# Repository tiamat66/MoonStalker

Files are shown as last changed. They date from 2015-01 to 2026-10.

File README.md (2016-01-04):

# MoonStalker

**Software for GoTo telescope control**

## Purpose

Project for GoTo telescope control consists of hardware and software. Software lives in this repository. There are two pieces of software.
 
The first called Drive is used on an arduino based platform that drives the hardwares GoTo feature and uses stepper motors.

The second piece called Control is Android based software that commands the Drive software and contains the user interface and logic.

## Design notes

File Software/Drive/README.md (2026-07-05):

# Drive

## Purpose

Drive is a software component installed on an Arduino Micro based hardware, which controls the stepper motors that rotate the telescope and provide GoTo and track functionality.

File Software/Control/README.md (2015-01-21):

# Control

## Purpose

Control is an Android application that communicates with an Arduino based hardware that drives the telescope. Communication between Android device and Arduino platform is performed over a Bluetooth connection.

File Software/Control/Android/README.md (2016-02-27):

# Android

## Purpose

Android application.
Includes an user friendly interface and module for Telescope positioning calculation.
It also includes module for Bluetooth connection with Arduino platform.

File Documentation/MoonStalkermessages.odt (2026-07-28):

MoonStalker messages

# Introduction

This document describes the messages being exchanged between the Android Control and the Arduino based Drive unit.

< - start message delimiter

> - end message delimiter

All messages exchanged must start with the start message delimiter and end with the end message delimiter, e.g. <BTRY?> to query the battery voltage. Carriage return '\r' and newline '\n' can be sent, but will be ignored and removed from the text stream. All text is ASCII encoded.

Android Control is the initiator of messages and Arduino Drive unit responds to the messages to acknowledge receipt and provide responses. The only exception are the error, warning and info messages, which can be sent to the Android Control unit unsolicited.

# Control messages

## Move

<MV a b s> IDLE -> WAITING

a - horizontal steps

b - vertical steps

s – maximum speed of the stepper in RPM

Move the telescope in horizontal and vertical direction. While RDY message is not returned from Arduino, all move actions made by MoonStalker are blocked. The maximum speed for the stepper motors is specified with s, e.g. 500 RPM.

Example:

<MV 1000 200 500>

Moves 1000 steps in horizontal and 200 steps in vertical. Horizontal will move with 500 RPM, vertical will move with 100 RPM, because it needs to execute five times less steps.

Response:

<MV_ACK a b s> - Start movement with the specified parameters WAITING -> MOVING

<RDY> - Finished moving to spec location, MOVING -> IDLE ... gre na ping receiver

## Move start

<MVS d s --> IDLE --> WAITING

d - direction (N, S, W, E, NW, NE, SW, SE)

s – speed in RPM, both horiz and vertical steppers move with this speed

Start moving the telescope in the specific direction. It keeps moving until MVE message is received or ERROR happens. Speed s is specified in RPM of the stepper motor.

Example:

<MVS NE 500>

Starts moving both horizontal and vertical stepper to move the telescope in NE direction (up and to the right), both steppers rotate with 500 RPM.

Response:

<MVS_ACK d s> - Start movement with the specified parameters WAITING -> MOVING

<NOT_RDY> - Drive unit is not currently executing MVS started movement

## Move end

<MVE> MOVING -> WAITING

Stop moving the telescope after started when MVS was received.

Response:

<NOT_RDY> - Drive unit is not currently executing MVS started movement

<MVE_ACK> - Stopping previously started MVS movement WAITING -> IDLE

# Status messages

## Status

<MVST?> -> WAITING

Get move status of the telescope, whether the telescope is still moving or if it is ready to accept new move command.

Response:

<RDY> - Drive unit is ready to accept new move command

<NOT_RDY> - Drive unit is still executing the previous move command and is not ready yet to accept new move commands

## Battery

<BTRY?>

Request to Arduino to return the battery voltage in mV.

Response:

<BTRY voltage>

voltage - value of the current voltage of Telescope battery in millivolts.

Reply from Arduino give information of current voltage of telescope battery.

# Error Messages

Error messages can be sent to the Android Control unit unsolicited.

<ERROR error_msg>

When something unexpected happens on telescope, the reason for error is returned from Arduino.

ERROR MESSAGE | MEANING
END_LIMIT_SW_TRIG | End limit switch has been triggered

# Warning messages

Warning messages can be sent to the Android Control unit unsolicited.

<WARNING warning_msg>

WARNING MESSAGE | MEANING
BTRY_LOW | Battery voltage is low

# Info messages

Info messages can be sent to the Android Control unit unsolicited.

Info messages can be anything and are only meant for logging purposes. The Control unit is not meant to execute any actions upon receiving them.

<INFO info_msg>

# Position messages

An azimuth and height in degrees are sent to FE app of current object

<POS pos_msg>

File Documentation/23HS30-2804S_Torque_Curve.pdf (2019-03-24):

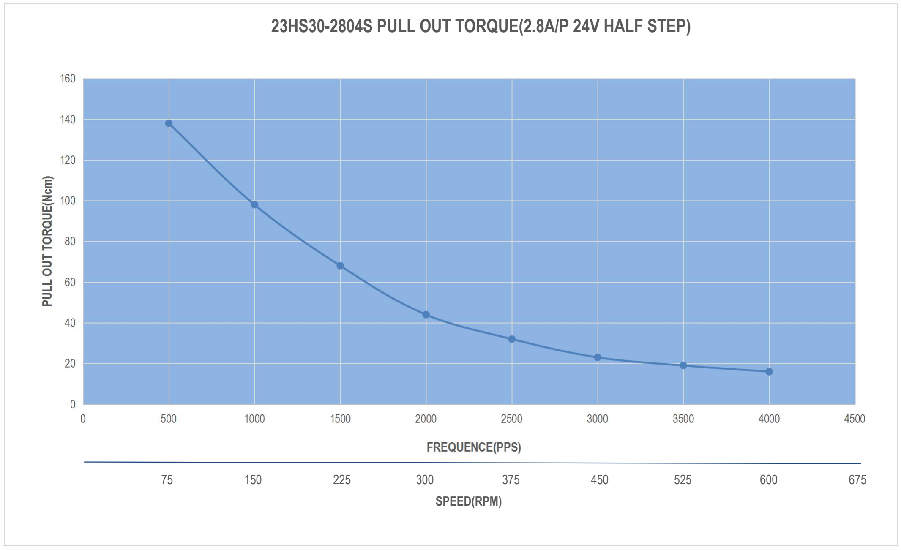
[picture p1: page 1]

23HS30-2804S PULL OUT TORQUE(2.8A/P 24V HALF STEP)

75 | 150 | 225 | 300 | 375 | 450 | 525 | 600 | 675
SPEED(RPM)

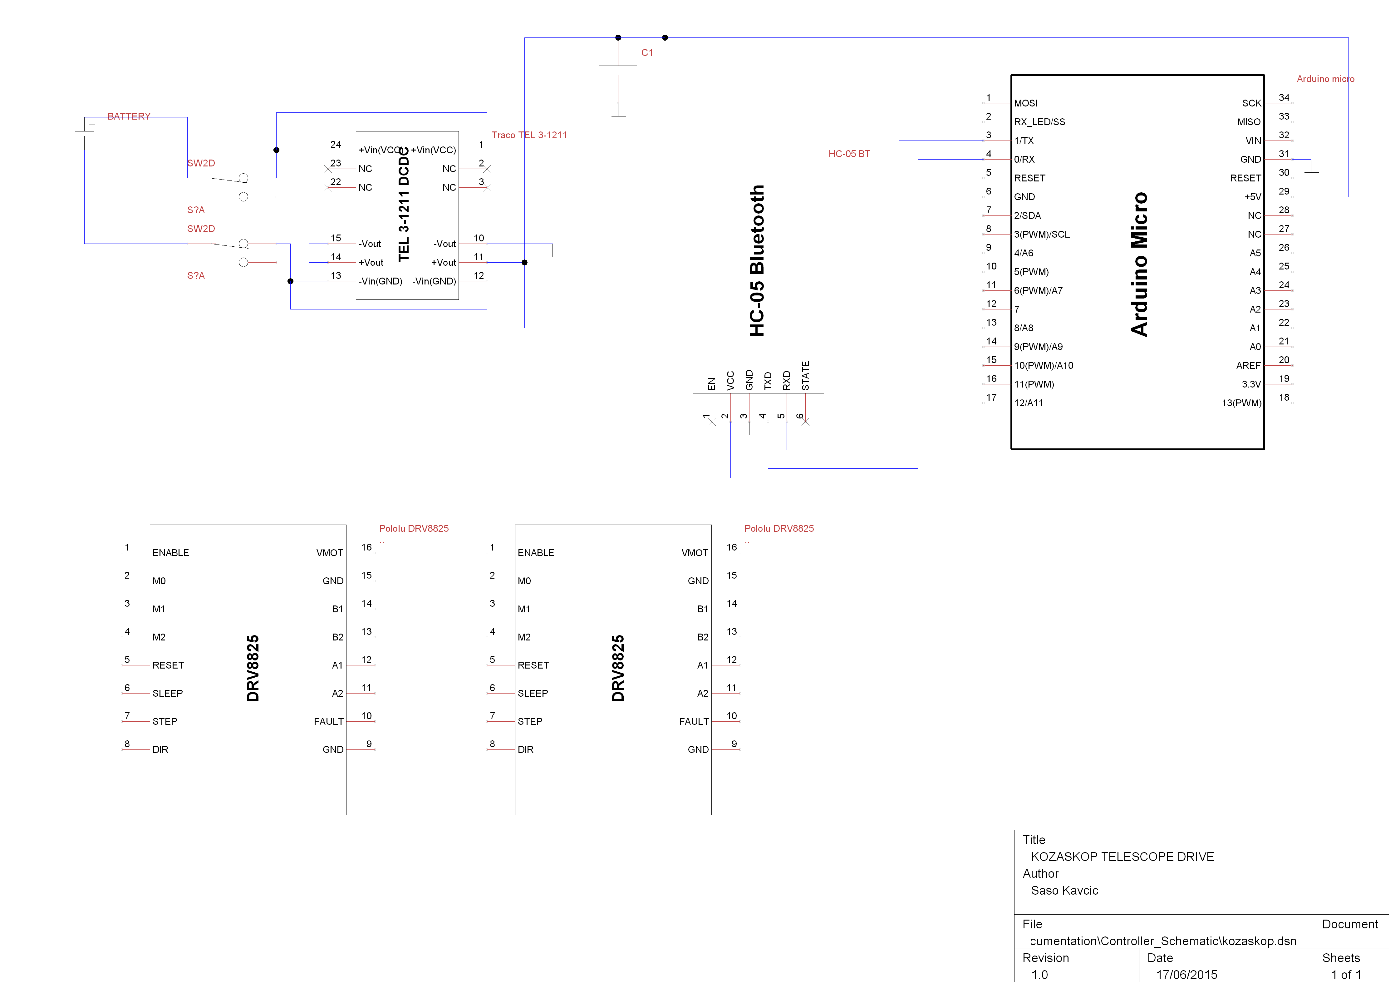
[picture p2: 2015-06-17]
Documentation/Controller_Schematic/kozaskop.png

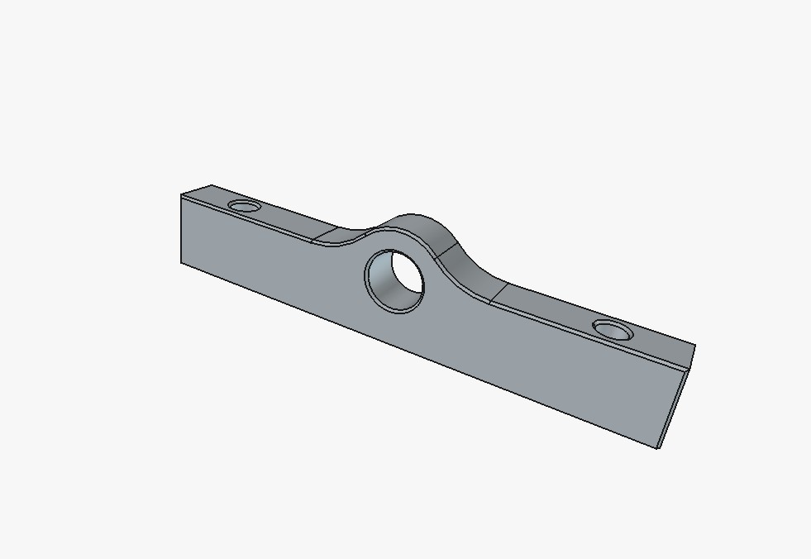
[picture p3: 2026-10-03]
CAD/tube_holder/tube_holder.jpeg

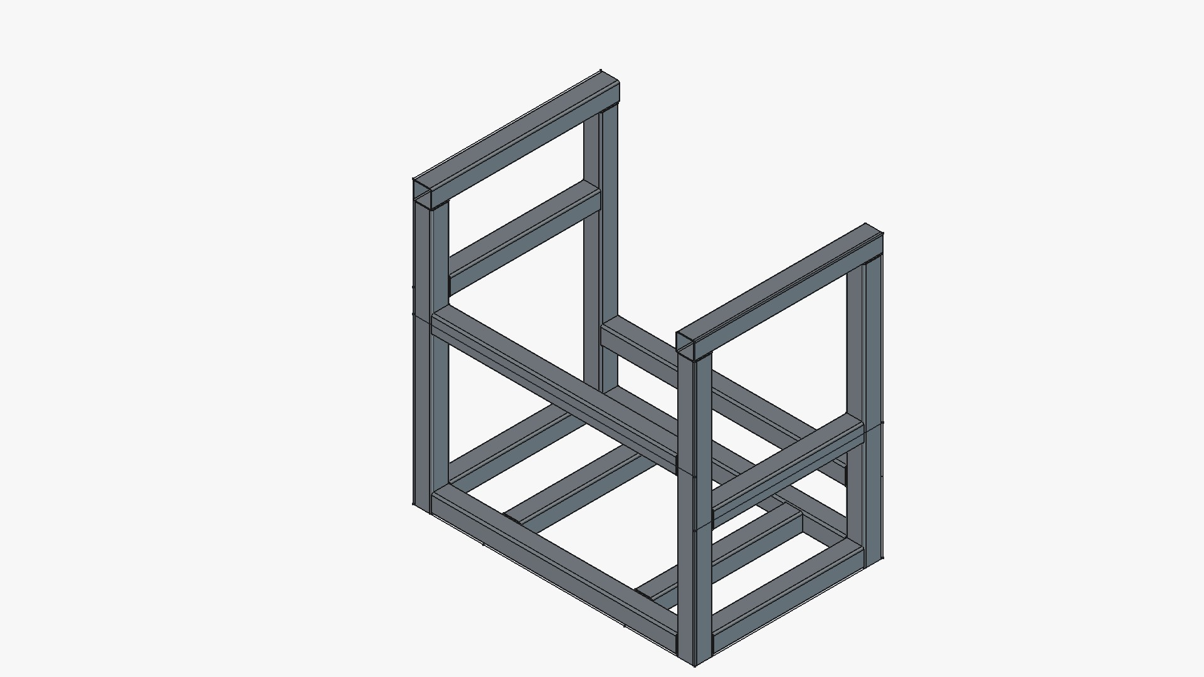
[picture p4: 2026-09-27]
CAD/upper_frame/upper_frame.jpeg

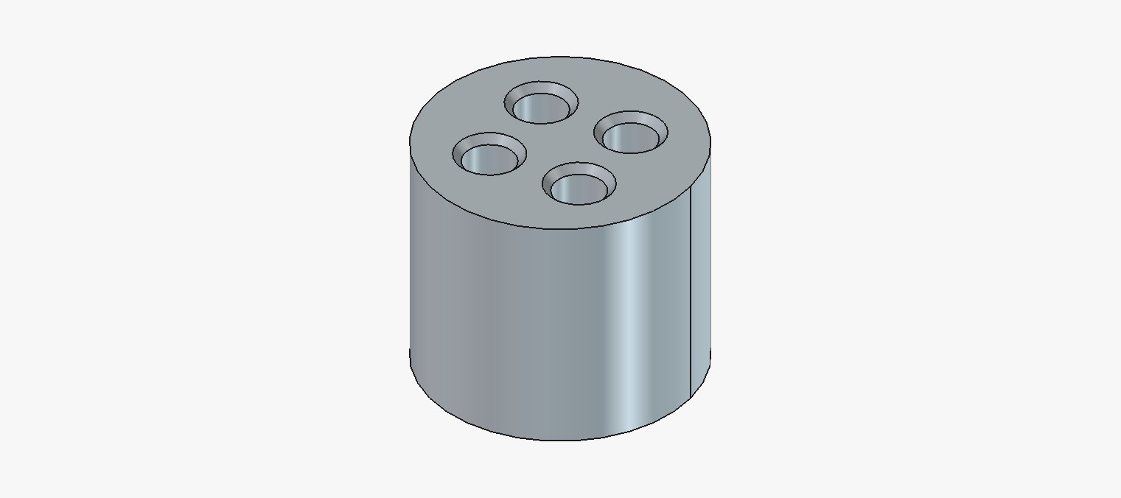
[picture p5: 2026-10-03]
CAD/spool/spool.jpeg

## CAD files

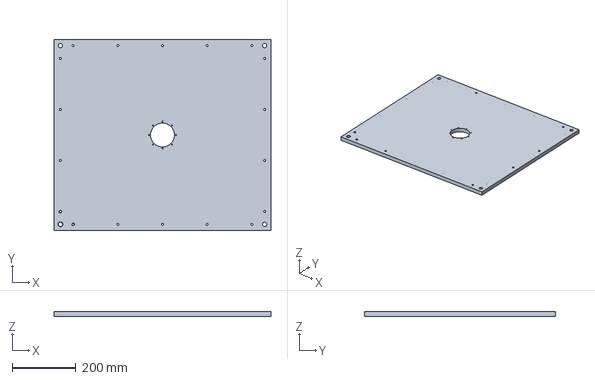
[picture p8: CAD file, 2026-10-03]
CAD/bottom_plate/bottom_plate.FCStd
680.0 x 600.0 x 15.0 mm

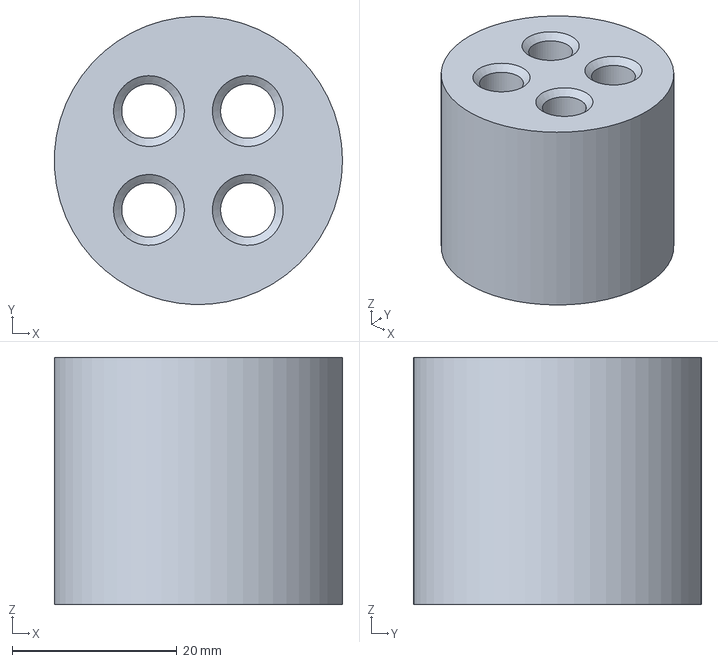
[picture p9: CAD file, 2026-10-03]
CAD/spool/spool.FCStd
35.0 x 35.0 x 30.0 mm

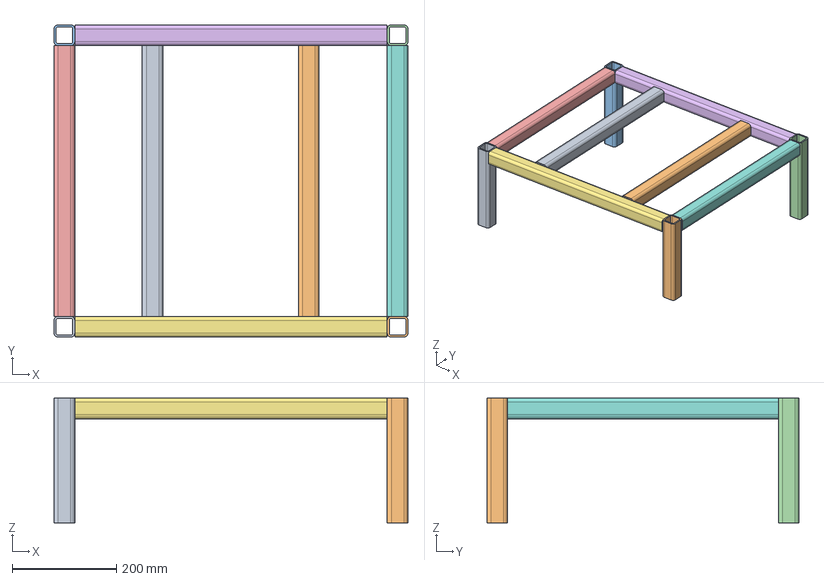
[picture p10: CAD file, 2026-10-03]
CAD/stand/stand.FCStd
680.0 x 600.0 x 240.0 mm
Profile_40x4_0_029
Profile_40x4_0_033
Profile_40x4_0_037
Profile_40x4_0_041
Profile_40x4_0_004_Tr_Tr
Profile_40x4_0_007_Tr_Tr
Profile_40x4_0_006_Tr_Tr
Profile_40x4_0_005_Tr_Tr
Profile_40x4_0_020_Tr
Profile_40x4_0_021_Tr

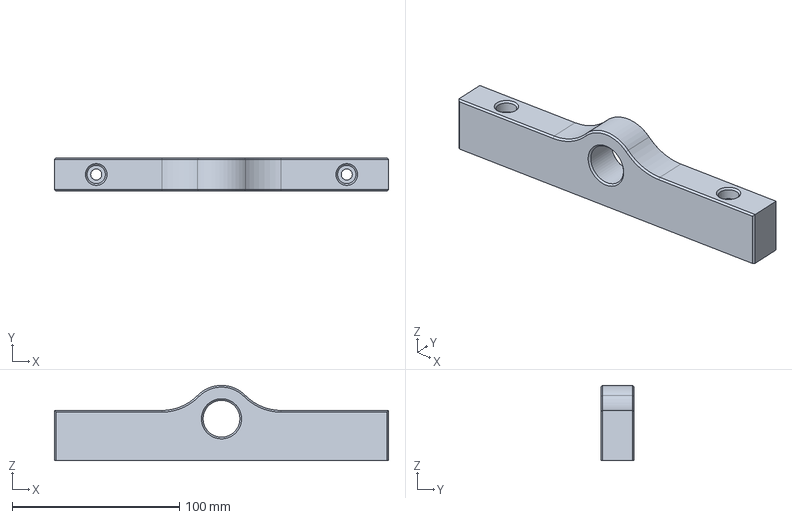
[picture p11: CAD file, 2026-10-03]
CAD/tube_holder/tube_holder.FCStd
200.0 x 20.0 x 45.0 mm

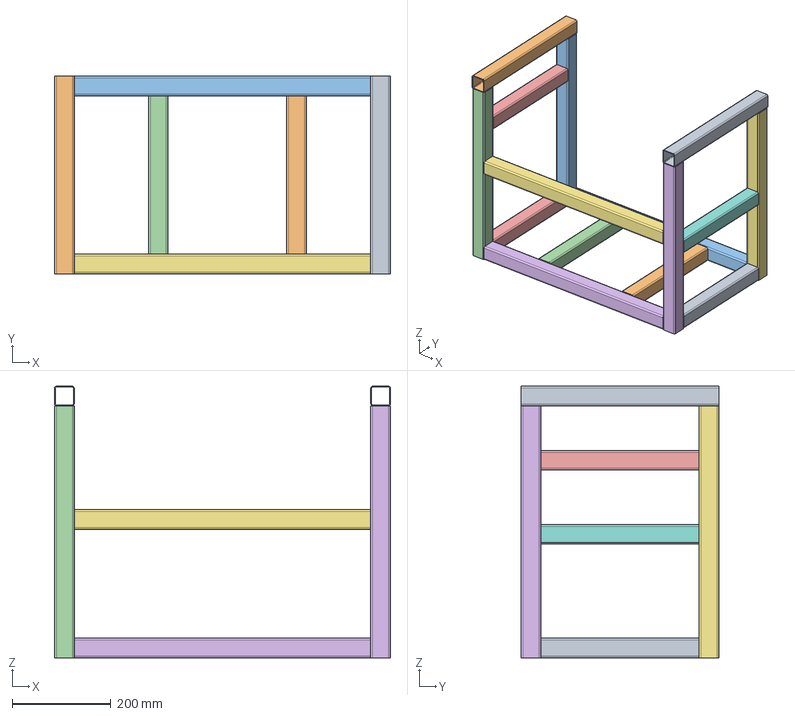
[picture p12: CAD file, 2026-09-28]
CAD/upper_frame/upper_frame.FCStd
680.0 x 400.0 x 550.0 mm
Profile_40x2_0_002
Profile_40x2_0_003
Profile_40x2_0_044_Tr
Profile_40x2_0_010_Tr
Profile_40x2_0_040_Tr_Tr001
Profile_40x2_0_011_Tr002
Profile_40x2_0_041_Tr_Tr001
Profile_40x2_0_043_Tr_Tr001
Profile_40x2_0_028_Tr_Tr002
Profile_40x2_0_031_Tr_Tr001
Profile_40x2_0_027_Tr_Tr001
Profile_40x2_0_030_Tr_Tr001
Profile_40x2_0_026_Tr_Tr001
Profile_40x2_0_029_Tr_Tr001
Profile_40x2_0_045_Tr

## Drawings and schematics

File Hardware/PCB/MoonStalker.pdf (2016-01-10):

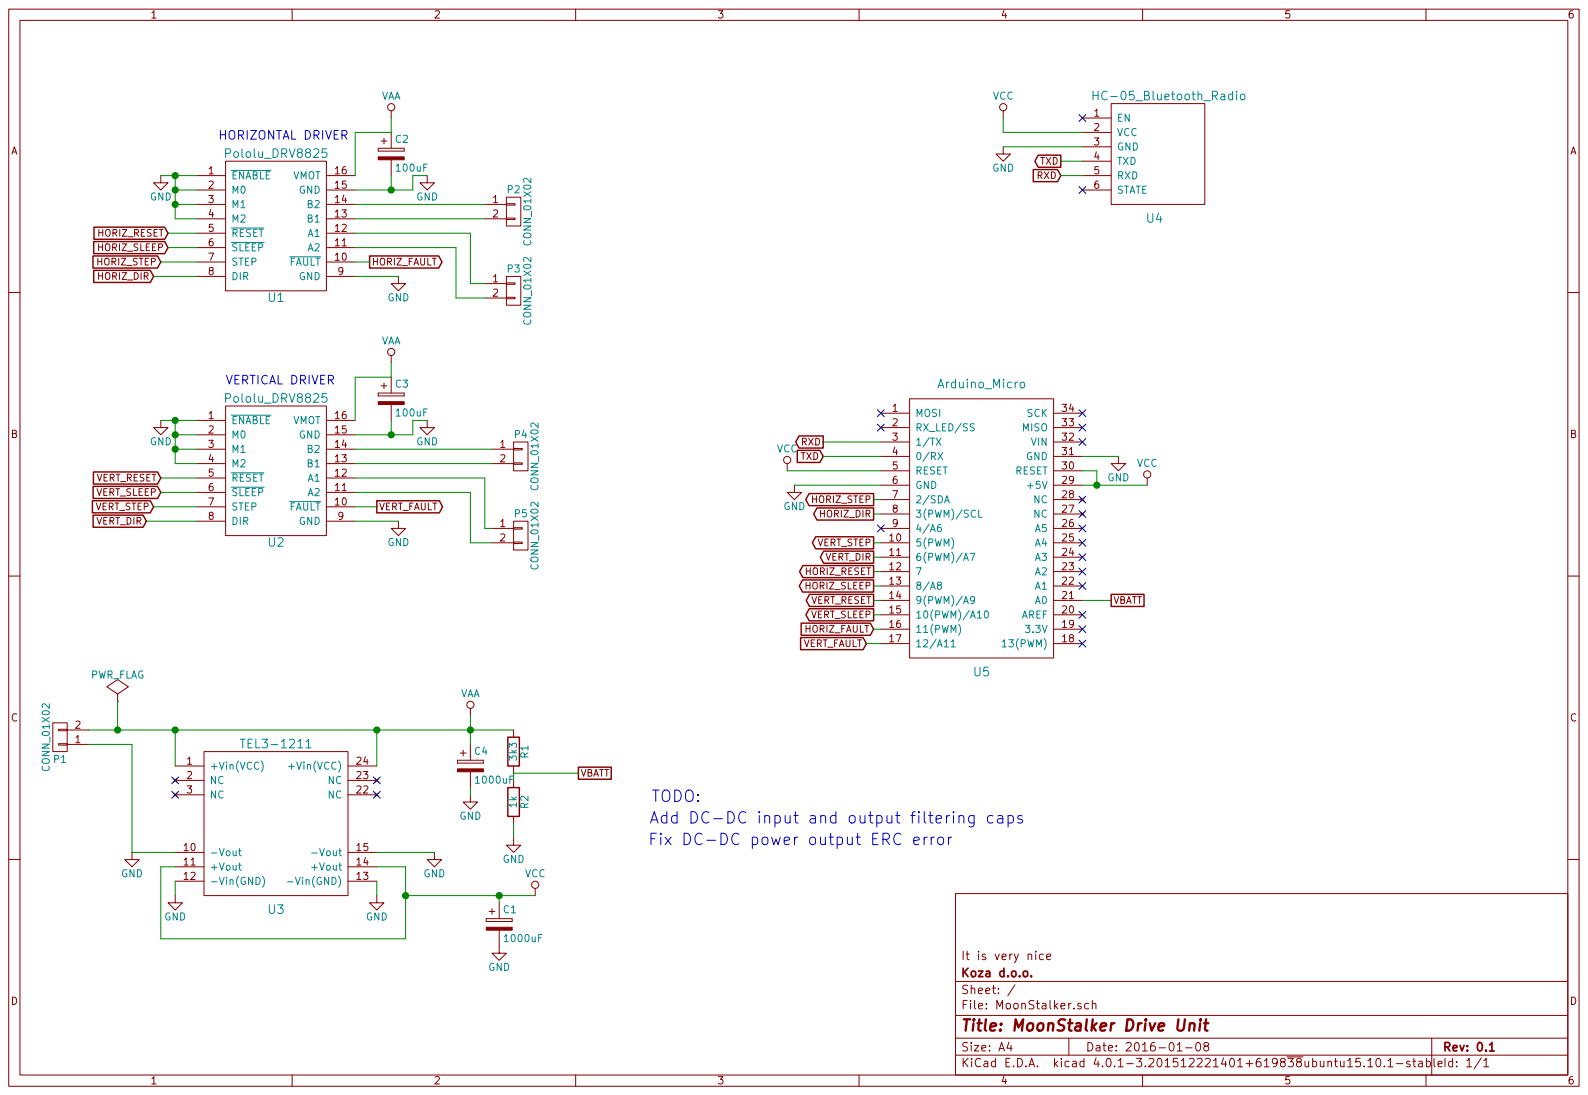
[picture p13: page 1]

Add DC-DC input and output filtering caps

Id: 1/1 Title: MoonStalker Drive Unit File: MoonStalker.sch Sheet: / Koza d.o.o.

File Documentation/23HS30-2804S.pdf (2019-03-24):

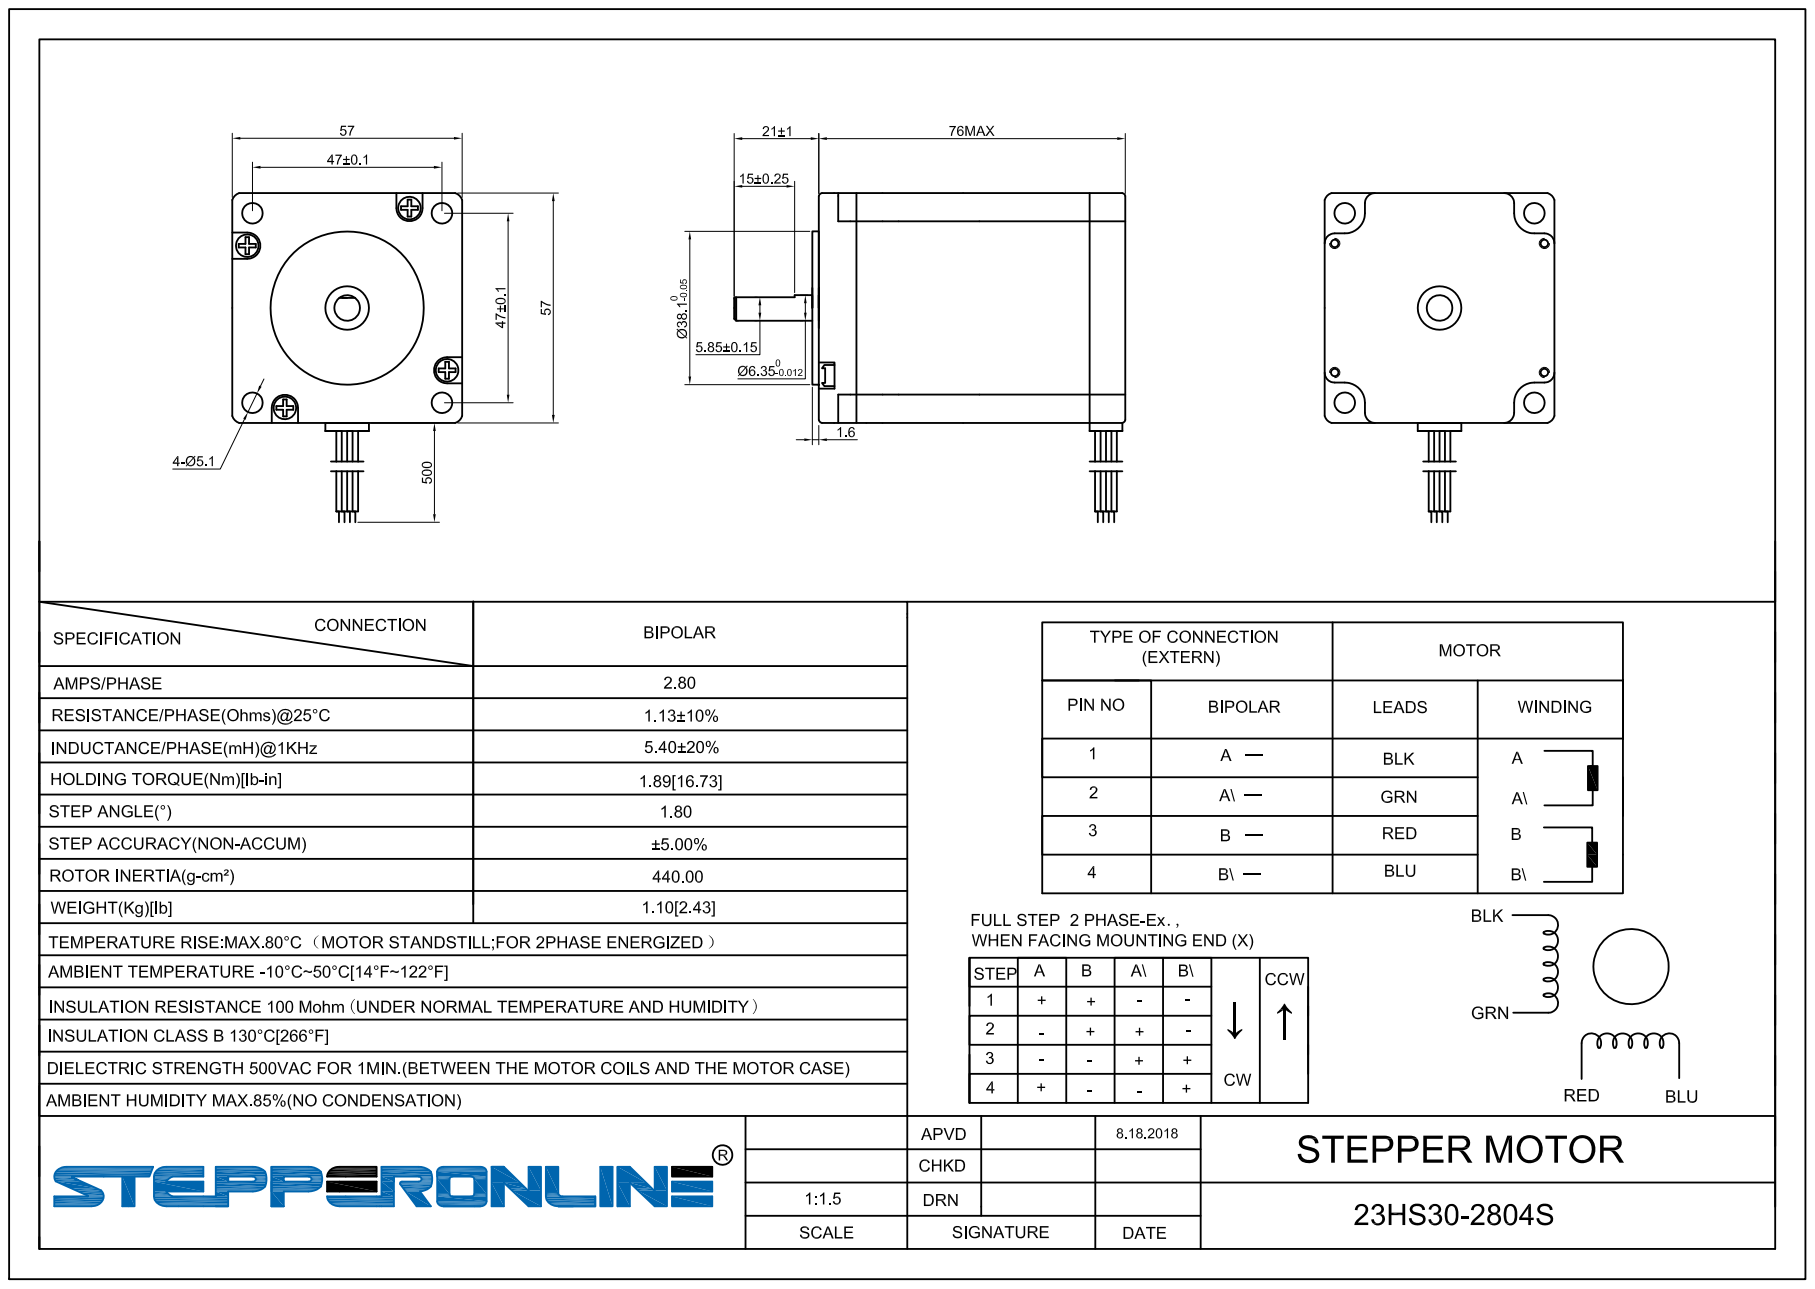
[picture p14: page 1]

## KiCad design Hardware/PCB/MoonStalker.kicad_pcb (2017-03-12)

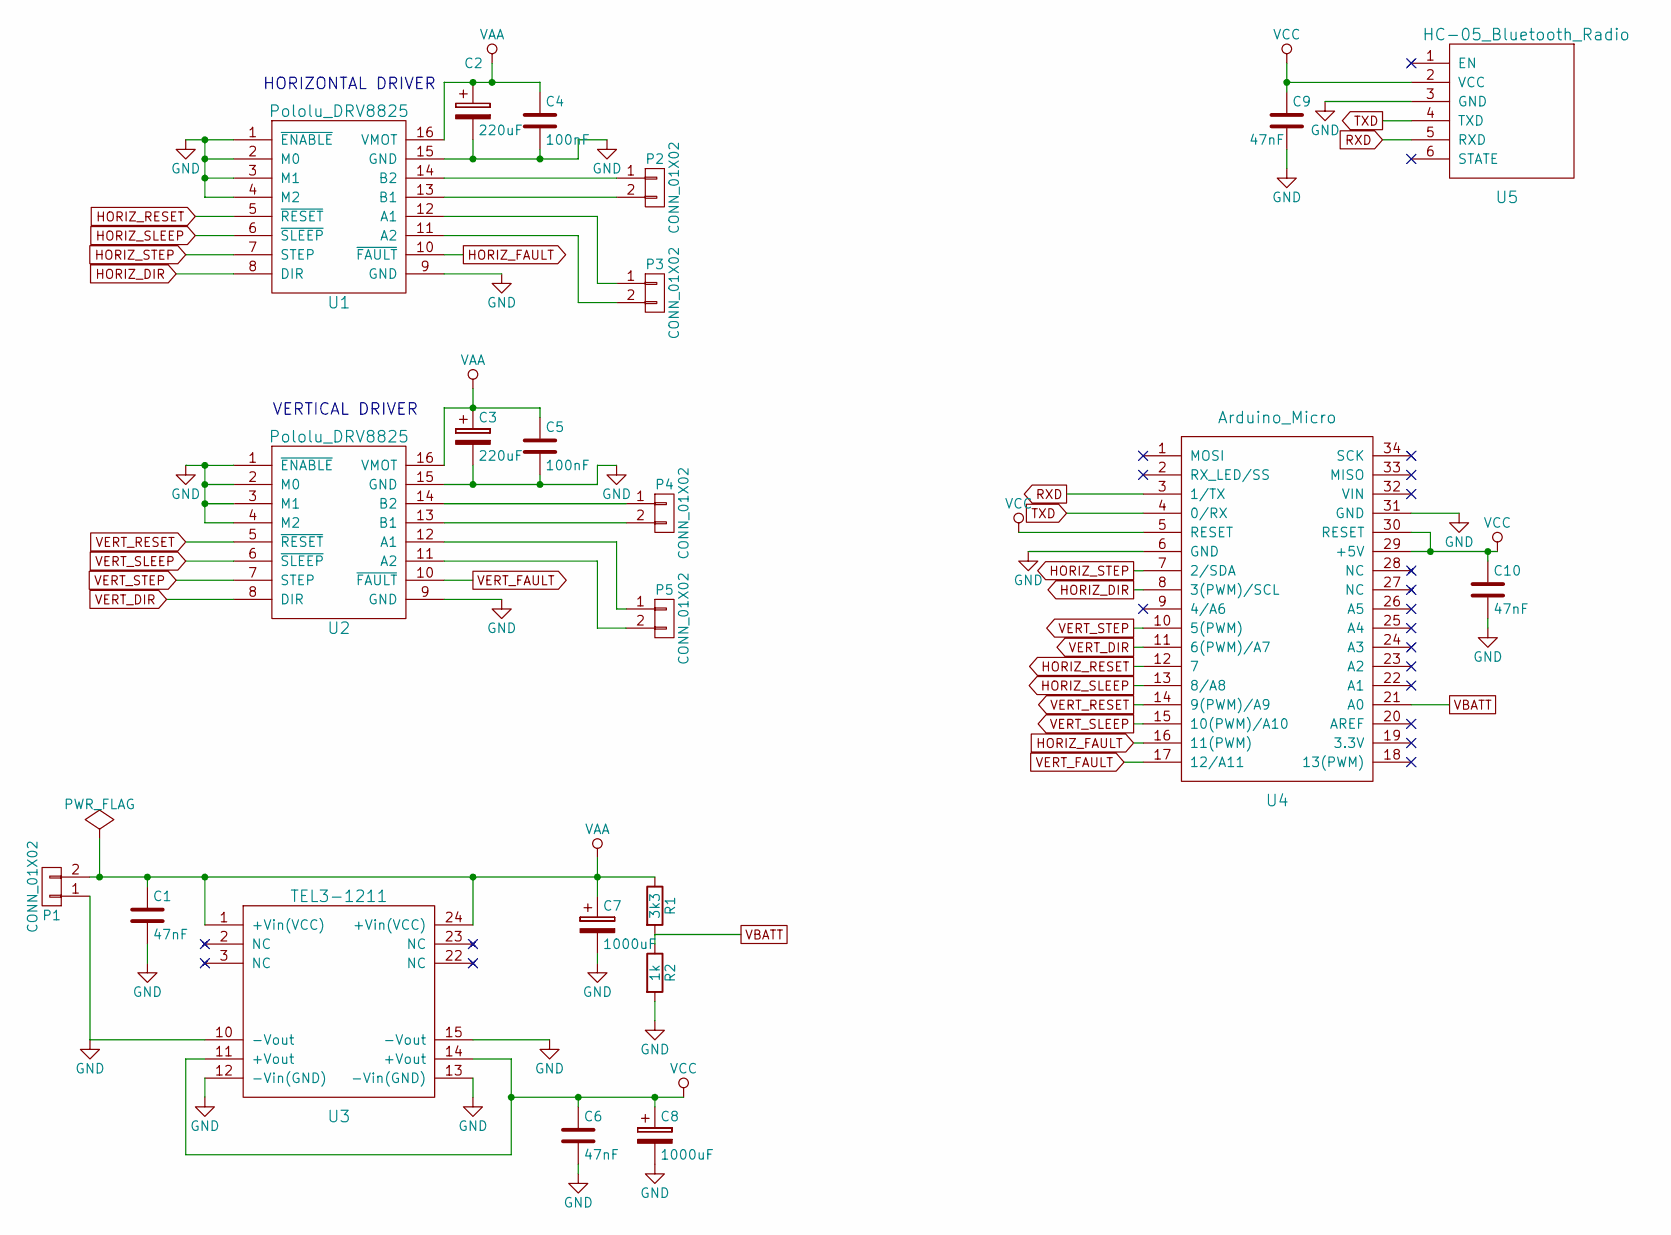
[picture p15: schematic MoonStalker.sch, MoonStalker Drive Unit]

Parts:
C1, C6, C10: 47nF; C_Rect_L13_W4_P10
C2, C3: 220uF; C_Radial_D10_L13_P5
C4, C5: 100nF; C_Rect_L7_W2.5_P5
C7, C8: 1000uF; C_Radial_D10_L16_P5
C9: 47nF; C_Rect_L10_W2.5_P7.5
P1, P2, P3, P4, P5: CONN_01X02; TerminalBlock_Pheonix_MPT-2.54mm_2pol
R1: 3k3; Resistor_Horizontal_RM7mm
R2: 1k; Resistor_Horizontal_RM7mm
U1, U2: Pololu_DRV8825
U3: TEL3-1211
U4: Arduino_Micro
U5: HC-05_Bluetooth_Radio; Socket_Strip_Straight_1x06

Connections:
GND: C1.2, C2.2, C3.2, C4.2, C5.2, C6.2, C7.2, C8.2, C9.2, C10.2, P1.1, R2.2, U1.1 (~ENABLE), U1.2 (M0), U1.3 (M1), U1.4 (M2), U1.9 (GND), U1.15 (GND), U2.1 (~ENABLE), U2.2 (M0), U2.3 (M1), U2.4 (M2), U2.9 (GND), U2.15 (GND), U3.10 (-Vout), U3.12 (-Vin(GND)), U3.13 (-Vin(GND)), U3.15 (-Vout), U4.6 (GND), U4.31 (GND), U5.3 (GND)
HORIZ_DIR: U1.8 (DIR), U4.8 (3(PWM)/SCL)
HORIZ_FAULT: U1.10 (~FAULT), U4.16 (11(PWM))
HORIZ_RESET: U1.5 (~RESET), U4.12 (7)
HORIZ_SLEEP: U1.6 (~SLEEP), U4.13 (8/A8)
HORIZ_STEP: U1.7 (STEP), U4.7 (2/SDA)
unnamed: P2.1, U1.14 (B2)
unnamed: P2.2, U1.13 (B1)
unnamed: P3.1, U1.12 (A1)
unnamed: P3.2, U1.11 (A2)
unnamed: P4.1, U2.14 (B2)
unnamed: P4.2, U2.13 (B1)
unnamed: P5.1, U2.12 (A1)
unnamed: P5.2, U2.11 (A2)
RXD: U4.3 (1/TX), U5.5 (RXD)
TXD: U4.4 (0/RX), U5.4 (TXD)
VAA: C1.1, C2.1, C3.1, C4.1, C5.1, C7.1, P1.2, R1.1, U1.16 (VMOT), U2.16 (VMOT), U3.1 (+Vin(VCC)), U3.24 (+Vin(VCC))
VBATT: R1.2, R2.1, U4.21 (A0)
VCC: C6.1, C8.1, C9.1, C10.1, U3.11 (+Vout), U3.14 (+Vout), U4.5 (RESET), U4.29 (+5V), U4.30 (RESET), U5.2 (VCC)
VERT_DIR: U2.8 (DIR), U4.11 (6(PWM)/A7)
VERT_FAULT: U2.10 (~FAULT), U4.17 (12/A11)
VERT_RESET: U2.5 (~RESET), U4.14 (9(PWM)/A9)
VERT_SLEEP: U2.6 (~SLEEP), U4.15 (10(PWM)/A10)
VERT_STEP: U2.7 (STEP), U4.10 (5(PWM))

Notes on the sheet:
HORIZONTAL DRIVER
VERTICAL DRIVER

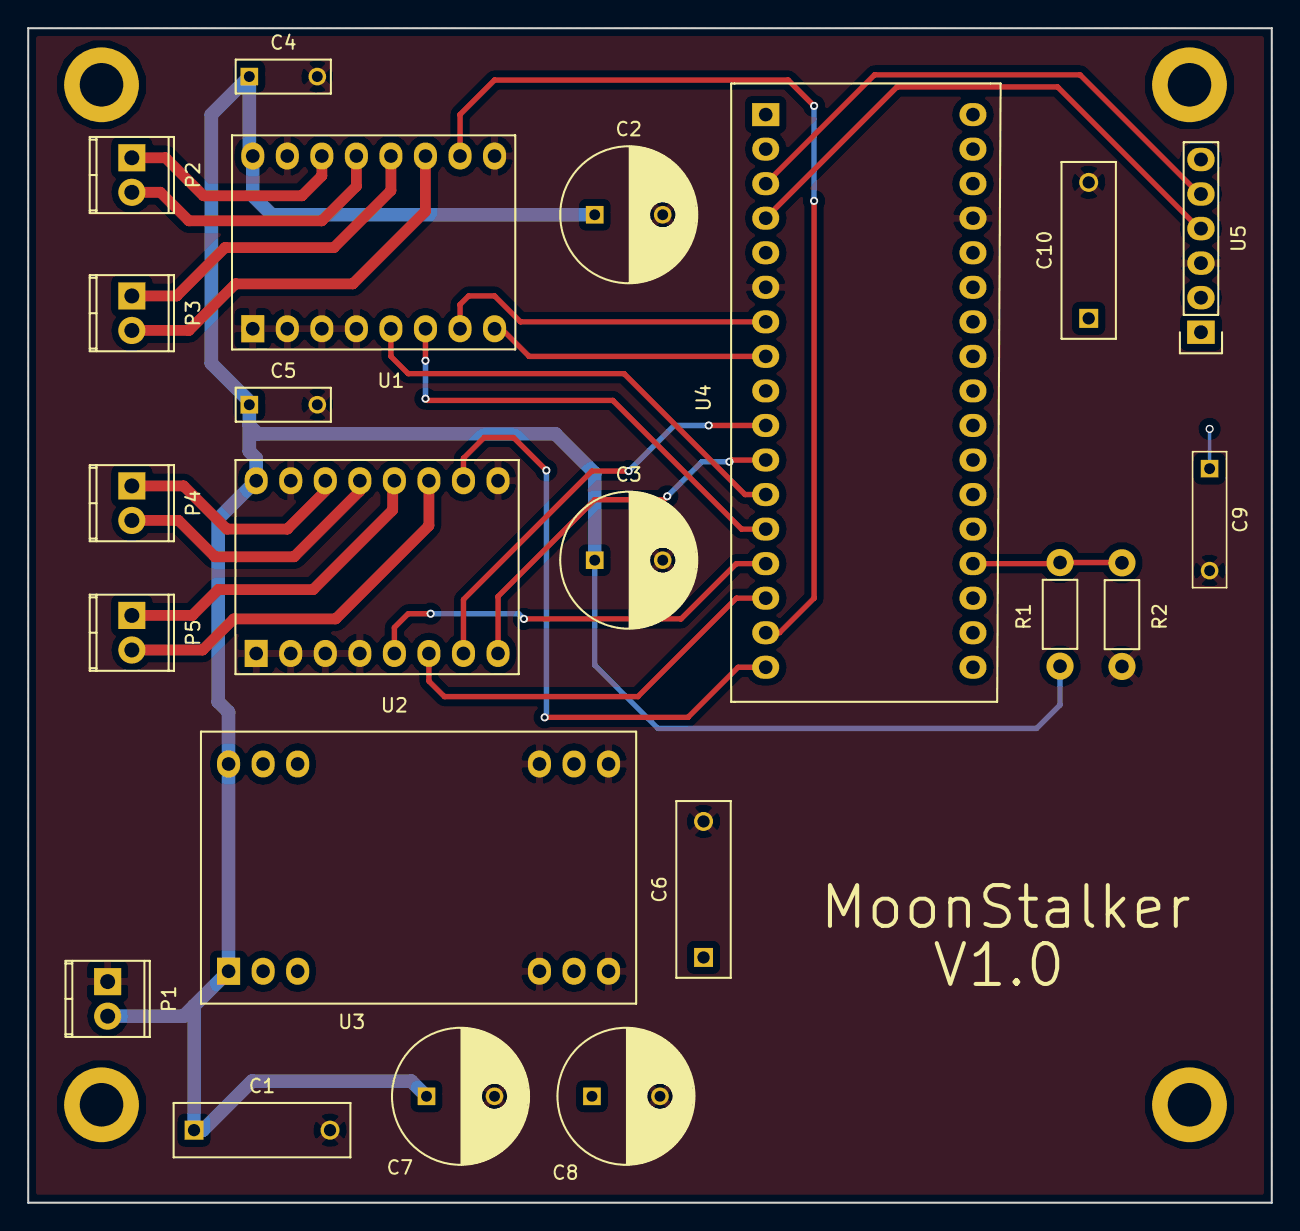
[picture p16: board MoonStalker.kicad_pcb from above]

Board: 2 copper layers, 91.4 x 86.4 mm, 22 parts (0 on the bottom side), 24 nets.

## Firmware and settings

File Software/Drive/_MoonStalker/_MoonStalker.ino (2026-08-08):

//  MoonStalker
//  SW for MoonStalker Drive unit control

//  Variable definitions

#include "StepperController.h"

// constants

const int BATTERY_LOW_LIMIT_MV = 10000;

// battery input pin
const int battery_voltage_pin = A0;


// output pins
const int horiz_step_pin = 2;
const int horiz_direction_pin = 3;
const int horiz_reset_pin = 7;
const int horiz_sleep_pin = 8;

const int vert_step_pin = 5;
const int vert_direction_pin = 6;
const int vert_reset_pin = 9;
const int vert_sleep_pin = 10;

// input pins
const int horiz_fault_pin = 11;
const int vert_fault_pin = 12;

// limit switch pins (normally open to GND, internal pull-up enabled)
// Direction mapping:
//   HORIZ_WEST  (A1) – blocks horizontal CW movement (telescope moving west / azimuth decreasing)
//   HORIZ_EAST  (A2) – blocks horizontal CCW movement (telescope moving east / azimuth increasing)
//   VERT_NORTH  (A3) – blocks vertical CW movement (telescope moving north / altitude increasing)
//   VERT_SOUTH  (A4) – blocks vertical CCW movement (telescope moving south / altitude decreasing)
const uint8_t LIMIT_HORIZ_WEST  = A1;
const uint8_t LIMIT_HORIZ_EAST  = A2;
const uint8_t LIMIT_VERT_NORTH  = A3;
const uint8_t LIMIT_VERT_SOUTH  = A4;

// global variables
StepperController stepper_controller = StepperController(200);

void setup()
{
    /* Open USB serial port */
  Serial.begin(115200);
  Serial.println("<INFO System start>");

  initialize_pins();

  // Initialize hardware timers for stepper pulse generation
  stepper_controller.initialize_timer1();
  stepper_controller.initialize_timer3();
}

void loop()
{
  static char command_buffer[65] = "";
  static int num_recv_char = 0;
  // Set after a receive buffer overflow: the rest of the oversized command
  // is thrown away one byte per loop() iteration until its terminator
  // arrives. Draining in the main loop (instead of spinning on
  // Serial.available()) keeps the limit switch watchdog running even if the
  // sender stalls mid-command.
  static bool discarding = false;

  if (Serial.available() > 0)
  {
    char incoming_char = Serial.read();

    if (discarding)
    {
      if (incoming_char == '>' || incoming_char == 10 || incoming_char == 13)
        discarding = false;
    }
    else if (num_recv_char >= 64)
    {
      Serial.println(F("<FATAL_ERROR RCV_BUFFER_OVERFLOW>"));
      // Reset the buffer and discard the remainder of the oversized command.
      // The truncated command is never executed.
      *command_buffer = 0;
      num_recv_char = 0;
      discarding = (incoming_char != '>' &&
                    incoming_char != 10 &&
                    incoming_char != 13);
    }
    // ignore newline characters
    else if ((incoming_char != 10) && (incoming_char != 13))
    {
      command_buffer[num_recv_char] = incoming_char;
      command_buffer[num_recv_char + 1] = 0;
      num_recv_char++;
      if (incoming_char == '>')
      {
        Serial.print("<INFO Handling command: ");
        Serial.print(command_buffer);
        Serial.println(">");
        handle_incoming_command(command_buffer);

        // clear command buffer, NULL terminate
        *command_buffer = 0;
        num_recv_char = 0;
      }
    }
  }

    // Poll limit switches every loop iteration
  check_limit_switches();

  // Check if free-run ramp-down has completed
  stepper_controller.check_free_run_complete();
}

int get_battery_voltage()
{
  uint16_t value = 0;
  uint32_t voltage_mv = 0;

  value = analogRead(battery_voltage_pin);
  // Voltage divider: R1 = 5088 Ohm, R2 = 14930 Ohm
  // Vbat_mV = ADC * (5000/1023) * (R1+R2)/R1
  //         = value * 5000 * (5088+14930) / (5088*1023)
  //
  // The multiplications are interleaved with the divisions so no
  // intermediate result exceeds 32 bits. Evaluating value*5000*20018
  // first would overflow uint32_t for any ADC reading above 42.
  // Worst-case intermediates below (value = 1023):
  //   1023 * 20018 = 20,478,414
  //   20,478,414 / 5088 * 5000 = 20,120,000
  // Both fit comfortably; the residual rounding error (~5 mV at 19.7 V)
  // is well under the ADC's own 4.9 mV per LSB quantisation.
  voltage_mv = (uint32_t)value * (5088UL + 14930UL) / 5088UL * 5000UL / 1023UL;

  return voltage_mv;
}


/* handle_incoming_command

   handle command tag that arrived
   over serial connection

   commands:
   <MV a b>
   <BTRY?>
   <MVST?>
   <ALARMS?>
   <DEBUG>
   <STOP>
   <MVS direction speed>
   <LIM?>
   <STEP_COUNTER?>
   <STEP_COUNTER_RESET>
   <COORDS?>

*/
void handle_incoming_command(char *command_buff)
{
  char command[65];
  char *cmd;

  // extract command without starting '<'
  // and ending '>'
  strcpy(command, command_buff + 1);
  size_t command_len = strlen(command);
  // Nothing between the brackets (e.g. "<>"): without this guard the
  // terminator strip below would write to command[-1].
  if (command_len == 0)
    return;
  command[command_len - 1] = 0;

  cmd = strtok(command, " ");
  // Empty command body, no token to dispatch on.
  if (cmd == NULL)
    return;

    if (!strcmp(cmd, "MV"))
  {
    char *horiz_steps_str;
    char *vert_steps_str;
    char *rpm_speed_str;
    int horiz_steps, vert_steps, rpm_speed;
    StepperDirection horiz_direction;
    StepperDirection vert_direction;

    if (stepper_controller.get_running_mode() != RunningMode::IDLE_MODE)
    {
      Serial.println("<MV_NACK NOT_RDY>");
      return;
    }
    horiz_steps_str = strtok(NULL, " ");
    vert_steps_str = strtok(NULL, " ");
    rpm_speed_str = strtok(NULL, " ");

    // strtok returns NULL for a missing parameter; passing that to atoi()
    // dereferences a null pointer.
    if (horiz_steps_str == NULL || vert_steps_str == NULL || rpm_speed_str == NULL)
    {
      Serial.println("<MV_NACK BAD_PARAMS>");
      return;
    }

    // Parse as long, then range check, so out-of-range input is rejected
    // rather than silently wrapping. The lower bound is -32767 and not
    // -32768 because the sign is stripped by negation below, and negating
    // INT16_MIN overflows.
    long horiz_steps_long = atol(horiz_steps_str);
    long vert_steps_long  = atol(vert_steps_str);
    long rpm_speed_long   = atol(rpm_speed_str);

    // A non-positive speed has no valid timer value; the axes would run at
    // whatever speed the previous move left configured.
    if (rpm_speed_long <= 0 || rpm_speed_long > 32767L ||
        horiz_steps_long < -32767L || horiz_steps_long > 32767L ||
        vert_steps_long  < -32767L || vert_steps_long  > 32767L)
    {
      Serial.println("<MV_NACK BAD_PARAMS>");
      return;
    }

    // Nothing to do. Passing this through would leave the controller stuck
    // in MOVE_MODE, because neither axis would ever step and so nothing
    // would return it to IDLE_MODE.
    if (horiz_steps_long == 0 && vert_steps_long == 0)
    {
      Serial.println("<MV_NACK NO_MOVEMENT>");
      return;
    }

    horiz_steps = (int)horiz_steps_long;
    vert_steps  = (int)vert_steps_long;
    rpm_speed   = (int)rpm_speed_long;

    Serial.print("<MV_ACK ");
    Serial.print(horiz_steps);
    Serial.print(" ");
    Serial.print(vert_steps);
    Serial.print(" ");
    Serial.print(rpm_speed);
    Serial.println(">");

    if (horiz_steps < 0)
    {
      horiz_steps = -horiz_steps;
      horiz_direction = StepperDirection::CCW;
    }
    else
    {
      horiz_direction = StepperDirection::CW;
    }
    if (vert_steps < 0)
    {
      vert_steps = -vert_steps;
      vert_direction = StepperDirection::CCW;
    }
        else
    {
      vert_direction = StepperDirection::CW;
    }

    // Check if movement is blocked by an active limit switch before starting the move.
    // Direction-to-limit mapping:
    //   Horizontal CW  (west)
    //     → blocked if LIMIT_HORIZ_WEST  is pressed (pin LOW)
    //   Horizontal CCW (east)
    //     → blocked if LIMIT_HORIZ_EAST  is pressed (pin LOW)
    //   Vertical CW    (north = altitude increasing)
    //     → blocked if LIMIT_VERT_NORTH  is pressed (pin LOW)
    //   Vertical CCW   (south = altitude decreasing)
    //     → blocked if LIMIT_VERT_SOUTH  is pressed (pin LOW)
    // If any axis would move toward a pressed limit, the entire command is rejected
    // before any movement starts.
    bool limit_blocked = false;
    if (horiz_steps > 0)
    {
      if (horiz_direction == StepperDirection::CW && digitalRead(LIMIT_HORIZ_WEST) == LOW)
        limit_blocked = true;
      else if (horiz_direction == StepperDirection::CCW && digitalRead(LIMIT_HORIZ_EAST) == LOW)
        limit_blocked = true;
    }
    if (vert_steps > 0)
    {
      if (vert_direction == StepperDirection::CW && digitalRead(LIMIT_VERT_NORTH) == LOW)
        limit_blocked = true;
      else if (vert_direction == StepperDirection::CCW && digitalRead(LIMIT_VERT_SOUTH) == LOW)
        limit_blocked = true;
    }
    if (limit_blocked)
    {
      Serial.println("<MV_NACK LIMIT_BLOCKED>");
      return;
    }

    stepper_controller.move_steppers(rpm_speed,
                                     horiz_direction,
                                     horiz_steps,
                                     rpm_speed,
                                     vert_direction,
                                     vert_steps);
  }
    else if (!strcmp(cmd, "MVS"))
  {
    char *direction_str;
    char *rpm_speed_str;
    int   rpm_speed;

        // Can only start free run from IDLE_MODE.
    // Must stop the current mode first (MV cannot be interrupted, free run
    // must be stopped before starting a new free run).
    if (stepper_controller.get_running_mode() != RunningMode::IDLE_MODE)
    {
      Serial.println("<MVS_NACK NOT_RDY>");
      return;
    }

    direction_str = strtok(NULL, " ");
    rpm_speed_str = strtok(NULL, " ");

    // strtok returns NULL for a missing parameter. A bare "<MVS>" would
    // otherwise reach strcmp(direction_str, "N") with a null pointer.
    if (direction_str == NULL || rpm_speed_str == NULL)
    {
      Serial.println("<MVS_NACK BAD_PARAMS>");
      return;
    }

    // A non-positive speed produces no valid timer value, so no axis would
    // actually start while the controller still entered FREE_RUN_MODE.
    long rpm_speed_long = atol(rpm_speed_str);
    if (rpm_speed_long <= 0 || rpm_speed_long > 32767L)
    {
      Serial.println("<MVS_NACK BAD_PARAMS>");
      return;
    }
    rpm_speed = (int)rpm_speed_long;

    // Check if movement is blocked by an active limit switch before starting free run.
    // Direction-to-limit mapping for MVS commands:
    //   N  (north  = vertical CW)    → blocked if LIMIT_VERT_NORTH  is pressed
    //   S  (south  = vertical CCW)   → blocked if LIMIT_VERT_SOUTH  is pressed
    //   W  (west   = horizontal CW)  → blocked if LIMIT_HORIZ_WEST  is pressed
    //   E  (east   = horizontal CCW) → blocked if LIMIT_HORIZ_EAST  is pressed
    //   NW (north-west)              → blocked if EITHER corresponding limit is pressed
    //   NE (north-east)              → blocked if EITHER corresponding limit is pressed
    //   SW (south-west)              → blocked if EITHER corresponding limit is pressed
    //   SE (south-east)              → blocked if EITHER corresponding limit is pressed
    // If the direction is blocked, the command is rejected with <MVS_NACK LIMIT_BLOCKED>
    // and no movement starts.
    bool limit_blocked = false;

    if (!strcmp(direction_str, "N"))
    {
      if (digitalRead(LIMIT_VERT_NORTH) == LOW) limit_blocked = true;
      if (!limit_blocked)
        stepper_controller.free_run_start(0, StepperDirection::IGNORE, rpm_speed, StepperDirection::CW);
    }
    else if (!strcmp(direction_str, "S"))
    {
      if (digitalRead(LIMIT_VERT_SOUTH) == LOW) limit_blocked = true;
      if (!limit_blocked)
        stepper_controller.free_run_start(0, StepperDirection::IGNORE, rpm_speed, StepperDirection::CCW);
    }
    else if (!strcmp(direction_str, "W"))
    {
      if (digitalRead(LIMIT_HORIZ_WEST) == LOW) limit_blocked = true;
      if (!limit_blocked)
        stepper_controller.free_run_start(rpm_speed, StepperDirection::CW, 0, StepperDirection::IGNORE);
    }
    else if (!strcmp(direction_str, "E"))
    {
      if (digitalRead(LIMIT_HORIZ_EAST) == LOW) limit_blocked = true;
      if (!limit_blocked)
        stepper_controller.free_run_start(rpm_speed, StepperDirection::CCW, 0, StepperDirection::IGNORE);
    }
    else if (!strcmp(direction_str, "NW"))
    {
      if (digitalRead(LIMIT_VERT_NORTH) == LOW || digitalRead(LIMIT_HORIZ_WEST) == LOW) limit_blocked = true;
      if (!limit_blocked)
        stepper_controller.free_run_start(rpm_speed, StepperDirection::CW, rpm_speed, StepperDirection::CW);
    }
    else if (!strcmp(direction_str, "NE"))
    {
      if (digitalRead(LIMIT_VERT_NORTH) == LOW || digitalRead(LIMIT_HORIZ_EAST) == LOW) limit_blocked = true;
      if (!limit_blocked)
        stepper_controller.free_run_start(rpm_speed, StepperDirection::CCW, rpm_speed, StepperDirection::CW);
    }
    else if (!strcmp(direction_str, "SW"))
    {
      if (digitalRead(LIMIT_VERT_SOUTH) == LOW || digitalRead(LIMIT_HORIZ_WEST) == LOW) limit_blocked = true;
      if (!limit_blocked)
        stepper_controller.free_run_start(rpm_speed, StepperDirection::CW, rpm_speed, StepperDirection::CCW);
    }
    else if (!strcmp(direction_str, "SE"))
    {
      if (digitalRead(LIMIT_VERT_SOUTH) == LOW || digitalRead(LIMIT_HORIZ_EAST) == LOW) limit_blocked = true;
      if (!limit_blocked)
        stepper_controller.free_run_start(rpm_speed, StepperDirection::CCW, rpm_speed, StepperDirection::CCW);
    }
    else
    {
      Serial.println("<MVS_NACK UNKNOWN_DIRECTION>");
      return;
    }

    if (limit_blocked)
    {
      Serial.println("<MVS_NACK LIMIT_BLOCKED>");
      return;
    }

    Serial.print("<MVS_ACK ");
    Serial.print(direction_str);
    Serial.print(" ");
    Serial.print(rpm_speed);
    Serial.println(">");
  }
    else if (!strcmp(cmd, "MVE"))
  {
    if (stepper_controller.get_running_mode() != RunningMode::FREE_RUN_MODE)
    {
      Serial.println("<MVE_NACK NOT_RDY>");
      return;
    }
    else
    {
      stepper_controller.free_run_stop();
      Serial.println("<MVE_ACK>");
    }
  }
  else if (!strcmp(cmd, "BTRY?"))
  {
    int volt_mv = get_battery_voltage();
    Serial.print("<BTRY ");
    Serial.print(volt_mv);
    Serial.println(">");
  }
    else if (!strcmp(cmd, "MVST?"))
  {
    RunningMode mode = stepper_controller.get_running_mode();

    if (mode == RunningMode::IDLE_MODE)
    {
      Serial.println("<MVST IDLE>");
    }
    else if (mode == RunningMode::MOVE_MODE)
    {
      Serial.println("<MVST MOVING>");
    }
    else if (mode == RunningMode::FREE_RUN_MODE)
    {
      Serial.println("<MVST FREE_RUN>");
    }
  }
    else if (!strcmp(cmd, "ALARMS?"))
  {
    check_alarms();
  }
  else if (!strcmp(cmd, "DEBUG"))
  {
    // Only show remaining and current steps for MOVE_MODE, not FREE_RUN_MODE
    // (free run uses 65535 steps_remain and the values are meaningless for debugging)
    if (stepper_controller.get_running_mode() != RunningMode::FREE_RUN_MODE)
    {
      Serial.print("<MV_REMAIN X: ");
      Serial.print(StepperController::horiz_steps_remain);
      Serial.print(" Y: ");
      Serial.print(StepperController::vert_steps_remain);
      Serial.println(">");
      Serial.print("<MV_CURRENT X: ");
      Serial.print(StepperController::horiz_steps_current);
      Serial.print(" Y: ");
      Serial.print(StepperController::vert_steps_current);
      Serial.println(">");
    }
    else
    {
      // Always answer, so a client waiting on a reply does not hang.
      Serial.println("<DEBUG_NA FREE_RUN>");
    }
  }
    else if (!strcmp(cmd, "STEP_COUNTER?"))
  {
    noInterrupts();
    uint32_t x = StepperController::step_counter_x;
    uint32_t y = StepperController::step_counter_y;
    interrupts();
    Serial.print("<STEP_COUNTER X:");
    Serial.print(x);
    Serial.print(" Y:");
    Serial.print(y);
    Serial.println(">");
  }
    else if (!strcmp(cmd, "STEP_COUNTER_RESET"))
  {
    noInterrupts();
    StepperController::step_counter_x = 0;
    StepperController::step_counter_y = 0;
    StepperController::coord_x = 0;
    StepperController::coord_y = 0;
    interrupts();
    Serial.println("<STEP_COUNTER_RESET_ACK>");
  }
    else if (!strcmp(cmd, "COORDS?"))
  {
    noInterrupts();
    int32_t x = StepperController::coord_x;
    int32_t y = StepperController::coord_y;
    interrupts();
    Serial.print("<COORDS X:");
    Serial.print(x);
    Serial.print(" Y:");
    Serial.print(y);
    Serial.println(">");
  }
    else if (!strcmp(cmd, "STOP"))
    {
      StepperController::emergency_stop();
      Serial.println("<STOP_ACK>");
    }
    else if (!strcmp(cmd, "LIM?"))
  {
    // Query and report the current state of all four limit switches over Bluetooth.
    // Format:  <LIM HORIZ_WEST horiz_east vert_north VERT_SOUTH>
    // Each switch name is printed in UPPERCASE if the limit is active (pressed / pin LOW),
    // or in lowercase if the limit is inactive (not pressed / pin HIGH).
    // This allows the user to quickly see which physical limits are currently triggered.
    //
    // In contrast to the emergency stop in check_limit_switches(), this command is
    // informational only – it does not stop the motors.
    bool horiz_west_active  = (digitalRead(LIMIT_HORIZ_WEST)  == LOW);
    bool horiz_east_active  = (digitalRead(LIMIT_HORIZ_EAST)  == LOW);
    bool vert_north_active  = (digitalRead(LIMIT_VERT_NORTH)  == LOW);
    bool vert_south_active  = (digitalRead(LIMIT_VERT_SOUTH)  == LOW);

    Serial.print("<LIM");
    if (horiz_west_active) Serial.print(" HORIZ_WEST");  else Serial.print(" horiz_west");
    if (horiz_east_active) Serial.print(" HORIZ_EAST");  else Serial.print(" horiz_east");
    if (vert_north_active) Serial.print(" VERT_NORTH");  else Serial.print(" vert_north");
    if (vert_south_active) Serial.print(" VERT_SOUTH");  else Serial.print(" vert_south");
    Serial.println(">");
  }
  else
  {
    // Unrecognised command tag. Always answer, so a client waiting on a
    // reply does not hang waiting for a response that will never come.
    Serial.print("<ERR UNKNOWN_COMMAND ");
    Serial.print(cmd);
    Serial.println(">");
  }
}

// Check for any error conditions and return alarms in a single response.
// Response format: <ALARMS [alarm1] [alarm2] ...>
//   ALARM_LOW_BTRY             : Present if battery voltage < 10000 mV
//   ALARM_DRV_HORIZ_FAULT      : Present if horizontal DRV fault pin is LOW
//   ALARM_DRV_VERT_FAULT       : Present if vertical DRV fault pin is LOW
//   ALARM_LIMIT_HORIZ_WEST_ACTIVE  : Present if horizontal west limit is pressed
//   ALARM_LIMIT_HORIZ_EAST_ACTIVE  : Present if horizontal east limit is pressed
//   ALARM_LIMIT_VERT_NORTH_ACTIVE  : Present if vertical north limit is pressed
//   ALARM_LIMIT_VERT_SOUTH_ACTIVE  : Present if vertical south limit is pressed
void check_alarms()
{
  int battery_volt_mv = get_battery_voltage();
  int horiz_fault = digitalRead(horiz_fault_pin);
  int vert_fault  = digitalRead(vert_fault_pin);

  bool horiz_west_active  = (digitalRead(LIMIT_HORIZ_WEST)  == LOW);
  bool horiz_east_active  = (digitalRead(LIMIT_HORIZ_EAST)  == LOW);
  bool vert_north_active  = (digitalRead(LIMIT_VERT_NORTH)  == LOW);
  bool vert_south_active  = (digitalRead(LIMIT_VERT_SOUTH)  == LOW);

  Serial.print("<ALARMS");

  if (battery_volt_mv < BATTERY_LOW_LIMIT_MV)
  {
    Serial.print(" ALARM_LOW_BTRY");
  }

  if (horiz_fault == LOW)
  {
    Serial.print(" ALARM_DRV_HORIZ_FAULT");
  }

  if (vert_fault == LOW)
  {
    Serial.print(" ALARM_DRV_VERT_FAULT");
  }

  if (horiz_west_active)
  {
    Serial.print(" ALARM_LIMIT_HORIZ_WEST_ACTIVE");
  }

  if (horiz_east_active)
  {
    Serial.print(" ALARM_LIMIT_HORIZ_EAST_ACTIVE");
  }

  if (vert_north_active)
  {
    Serial.print(" ALARM_LIMIT_VERT_NORTH_ACTIVE");
  }

  if (vert_south_active)
  {
    Serial.print(" ALARM_LIMIT_VERT_SOUTH_ACTIVE");
  }

  Serial.println(">");
}

void initialize_pins()
{
  // output pins horizontal
  pinMode(horiz_step_pin, OUTPUT);
  pinMode(horiz_direction_pin, OUTPUT);
  pinMode(horiz_reset_pin, OUTPUT);
  pinMode(horiz_sleep_pin, OUTPUT);

  // output pins vertical
  pinMode(vert_step_pin, OUTPUT);
  pinMode(vert_direction_pin, OUTPUT);
  pinMode(vert_reset_pin, OUTPUT);
  pinMode(vert_sleep_pin, OUTPUT);

    // input fault pins
  pinMode(horiz_fault_pin, INPUT);
  pinMode(vert_fault_pin, INPUT);

  pinMode(battery_voltage_pin, INPUT);

    // limit switches (normally open to GND, internal pull-up)
  // When a switch is pressed, the pin reads LOW, indicating the physical limit is reached.
  // The internal pull-up keeps the pin HIGH when the switch is not pressed.
  pinMode(LIMIT_HORIZ_WEST,  INPUT_PULLUP);
  pinMode(LIMIT_HORIZ_EAST,  INPUT_PULLUP);
  pinMode(LIMIT_VERT_NORTH,  INPUT_PULLUP);
  pinMode(LIMIT_VERT_SOUTH,  INPUT_PULLUP);

  // set sleep pins
  digitalWrite(horiz_sleep_pin, HIGH);
  digitalWrite(vert_sleep_pin, HIGH);

    // set reset pins
  digitalWrite(horiz_reset_pin, HIGH);
  digitalWrite(vert_reset_pin, HIGH);
}
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

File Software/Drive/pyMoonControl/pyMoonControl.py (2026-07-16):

#!/usr/bin/env python3
"""
pyMoonControl - A GUI application to control MoonStalker Drive Unit
over serial communication with an Arduino Micro.

Requires: PySide6, pyserial
"""

import sys
import serial
import serial.tools.list_ports
from PySide6.QtWidgets import (
    QApplication, QMainWindow, QWidget, QVBoxLayout, QHBoxLayout,
    QGridLayout, QGroupBox, QPushButton, QLabel, QLineEdit,
    QTextEdit, QComboBox, QSpinBox, QMessageBox
)
from PySide6.QtCore import Qt, QThread, Signal, QTimer
from PySide6.QtGui import QFont


# ============================================================================
# Serial Thread
# ============================================================================

class SerialThread(QThread):
    """Background thread for reading serial data without blocking the GUI."""
    data_received = Signal(str)
    connection_status = Signal(bool)

    def __init__(self, parent=None):
        super().__init__(parent)
        self.serial_port = None
        self.running = False

    def connect_port(self, port_name: str, baud: int = 115200):
        """Open and configure the serial port."""
        if self.serial_port and self.serial_port.is_open:
            self.disconnect_port()
        try:
            self.serial_port = serial.Serial(
                port=port_name,
                baudrate=baud,
                bytesize=serial.EIGHTBITS,
                parity=serial.PARITY_NONE,
                stopbits=serial.STOPBITS_ONE,
                timeout=0.1
            )
            self.running = True
            self.connection_status.emit(True)
            if not self.isRunning():
                self.start()
        except Exception as e:
            self.connection_status.emit(False)
            raise e

    def disconnect_port(self):
        """Close the serial port."""
        self.running = False
        if self.serial_port and self.serial_port.is_open:
            try:
                self.serial_port.close()
            except Exception:
                pass
        self.serial_port = None
        self.connection_status.emit(False)

    def send_command(self, command: str):
        """Send a command string over serial."""
        if self.serial_port and self.serial_port.is_open:
            try:
                self.serial_port.write(command.encode('utf-8'))
                return True
            except Exception as e:
                print(f"Send error: {e}")
                return False
        return False

    def run(self):
        """Continuously read from the serial port."""
        buffer = ""
        while self.running:
            if self.serial_port and self.serial_port.is_open:
                try:
                    if self.serial_port.in_waiting > 0:
                        data = self.serial_port.read(self.serial_port.in_waiting)
                        buffer += data.decode('utf-8', errors='replace')
                        # Process complete lines (ending with '>')
                        while '>' in buffer:
                            line, buffer = buffer.split('>', 1)
                            line = line.strip()
                            if line:
                                # Re-add the closing bracket for display
                                self.data_received.emit(line + '>')
                except Exception as e:
                    print(f"Read error: {e}")
            else:
                self.msleep(10)

    def stop(self):
        """Stop the thread safely."""
        self.running = False
        self.wait()


# ============================================================================
# Serial Port Selector Widget
# ============================================================================

class SerialPortSelector(QWidget):
    """A widget for selecting and connecting to a serial port."""
    port_changed = Signal(str, int)

    def __init__(self, parent=None):
        super().__init__(parent)
        self.build_ui()
        self.refresh_ports()
        # Auto-refresh ports every 2 seconds
        self.refresh_timer = QTimer(self)
        self.refresh_timer.timeout.connect(self.refresh_ports)
        self.refresh_timer.start(2000)

    def build_ui(self):
        layout = QHBoxLayout(self)
        layout.setContentsMargins(0, 0, 0, 0)

        self.port_combo = QComboBox()
        self.port_combo.setMinimumWidth(200)
        self.port_combo.currentIndexChanged.connect(self.on_port_changed)
        layout.addWidget(QLabel("Port:"))
        layout.addWidget(self.port_combo)

        self.baud_combo = QComboBox()
        self.baud_combo.addItems(["9600", "19200", "38400", "57600", "115200", "230400"])
        self.baud_combo.setCurrentText("115200")
        layout.addWidget(QLabel("Baud:"))
        layout.addWidget(self.baud_combo)

        self.connect_btn = QPushButton("Connect")
        self.connect_btn.setAutoDefault(False)
        self.connect_btn.clicked.connect(self.toggle_connection)
        layout.addWidget(self.connect_btn)

        self.status_label = QLabel("Disconnected")
        self.status_label.setStyleSheet("color: red; font-weight: bold;")
        layout.addWidget(self.status_label)

        layout.addStretch()

    def refresh_ports(self):
        """Refresh the list of available serial ports."""
        current = self.port_combo.currentText()
        self.port_combo.blockSignals(True)
        self.port_combo.clear()
        ports = serial.tools.list_ports.comports()
        if ports:
            for port in sorted(ports, key=lambda p: p.device):
                desc = f"{port.device} - {port.description}" if port.description else port.device
                self.port_combo.addItem(desc, port.device)
            # Try to restore previous selection
            idx = self.port_combo.findText(current)
            if idx >= 0:
                self.port_combo.setCurrentIndex(idx)
        else:
            self.port_combo.addItem("No ports found", None)
        self.port_combo.blockSignals(False)

    def on_port_changed(self):
        pass

    def toggle_connection(self):
        if self.connect_btn.text() == "Connect":
            self.do_connect()
        else:
            self.do_disconnect()

    def do_connect(self):
        port_data = self.port_combo.currentData()
        if not port_data:
            QMessageBox.warning(self, "Connection Error", "No serial port selected.")
            return
        baud = int(self.baud_combo.currentText())
        self.port_changed.emit(port_data, baud)

    def do_disconnect(self):
        self.port_changed.emit("", 0)
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

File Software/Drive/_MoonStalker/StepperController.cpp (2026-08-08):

// ============================================================================
// StepperController.cpp
// ============================================================================
// Implements stepper motor control for the MoonStalker telescope drive.
// Two independent stepper motors (horizontal/azimuth, vertical/altitude) are
// driven by hardware timers on the ATmega32u4 (Arduino Micro):
//
//   Horizontal (azimuth): Timer1, output on pin 2 (PORTD, bit 1 = PD1)
//   Vertical  (altitude): Timer3, output on pin 5 (PORTC, bit 6 = PC6)
//
// Timer configuration:
//   - CTC mode (Clear Timer on Compare Match)
//   - 1/64 prescaler: timer clock = 16 MHz / 64 = 250 kHz = 4 us/tick
//   - OCRxA sets the step rate (half-period between steps)
//   - OCRxB generates a short pulse (~4 us) via COMPB compare match
//
// Step pulse generation sequence:
//   1. COMPA fires -> set step pin HIGH, decrement steps_remain
//   2. COMPB fires ~4 us later -> set step pin LOW
//   3. Next COMPA fires after OCRxA ticks -> repeat
//
// Ramping: Linear interpolation between start_OCR (slow) and target_OCR
//   (fast) over ramp_steps at both the beginning and end of a move.
//
// Sync mode: The axis with fewer steps has its OCR scaled proportionally
//   so both axes complete at the same time.
// ============================================================================

#include "StepperController.h"
#include "Arduino.h"

// ============================================================================
// Static member definitions
// ============================================================================
// These are declared as 'static volatile' in the header so they can be
// accessed from ISR context. They must be instantiated here in the .cpp
// to allocate storage.
//
// Steps remaining/tracking:
//   horiz_steps_remain / vert_steps_remain
//       Counted down in the ISR each time a step pulse is generated.
//       When zero, the COMPA interrupt is disabled to stop further pulses.
//   horiz_steps_current / vert_steps_current
//       Counted up in the ISR. Provides a monotonically increasing step
//       index for ramp position calculation. Also exposed via DEBUG command.
//   horiz_direction_state / vert_direction_state
//       Stores the current direction for each axis. Written by move_steppers()
//       and free_run_start(), used in the ISR for context.
volatile uint16_t StepperController::horiz_steps_remain = 0;
volatile uint16_t StepperController::vert_steps_remain = 0;

volatile uint16_t StepperController::horiz_steps_current = 0;
volatile uint16_t StepperController::vert_steps_current = 0;

volatile StepperDirection StepperController::horiz_direction_state = StepperDirection::CW;
volatile StepperDirection StepperController::vert_direction_state = StepperDirection::CW;

// Ramping and sync state:
//   ramp_steps_horiz/vert - Number of steps for the ramp phase on each axis.
//       Calculated in move_steppers() as min(ramp_steps, total_steps/2).
//   target_ocr_horiz/vert_isr - The steady-state OCR value to ramp toward.
//       Already adjusted for sync mode scaling before being stored here.
//   start_ocr_horiz/vert_isr - The slow-speed OCR value at ramp start.
//       Fixed at MAX_OCR_RAMP (2000 ticks ~ 8 ms between steps).
//   sync_mode_enabled - True if set_sync_mode(true) was called.
volatile uint16_t StepperController::ramp_steps_horiz = 0;
volatile uint16_t StepperController::ramp_steps_vert = 0;
volatile uint16_t StepperController::target_ocr_horiz_isr = 0;
volatile uint16_t StepperController::target_ocr_vert_isr = 0;
volatile uint16_t StepperController::start_ocr_horiz_isr = 0;
volatile uint16_t StepperController::start_ocr_vert_isr = 0;
volatile bool StepperController::sync_mode_enabled = true;
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

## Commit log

2015-02-25 An example for how to drive the motor simply
2015-04-15 Added tinycad library for arduino micro
2015-06-15 Added new symbol for DRV8825 and pdf. Added dsn for kozaskop
    [kozaskop.dsn]
2015-06-17 Created more custom parts in tinycad and more schematic completed
    [kozaskop.dsn]
2015-12-29 Added a new kicad project for pcb
    [kozaskop.kicad_pcb, kozaskop.sch]
2016-01-05 Deleted Hardware
    [kozaskop.kicad_pcb, kozaskop.sch]
2016-01-06 Started creating kicad schematic, created arduino and pololu drv stepper driver parts
    [MoonStalker.kicad_pcb, MoonStalker.sch]
2016-01-07 Added components for DCDC converter and BlueTooth radio
    [MoonStalker.sch]
2016-01-10 Added a few more connections to the schematic
    [MoonStalker.sch]
2016-01-10 Schematic is now almost complete. An error with DCDC converter power output ports must be fixed and input and output filtering capacitors must be added. Pdf schematic has also been generated.
    [MoonStalker.sch]
2016-01-10 Fixed some of the power port problems, only one problem remains now.
    [MoonStalker.sch]
2016-01-12 Added a few decoupling caps to schematic
    [MoonStalker.sch]
2016-02-28 Created PCB footprint for TEL3-1211 DC-DC converter. Fixed power output ERC error in the schematic.
    [MoonStalker.sch]
2016-02-29 Added few debug printouts
2016-03-11 Android: Implemented Trace thread. Updated Control
2016-03-11 Android: Added debug Emulator for Arduino
2016-03-12 Android: Added button widgets
2016-03-13 Android: Fixed Trace on/Trace off actions.
2016-03-14 Android: Added simple Arduino emulator, for BT testing
2016-03-15 Android: Implemented message listener from Arduino
2016-03-21 Android: Fixed bug in Message for Battery Voltage
2016-03-28 Fixed TEL3-1211 footprint and removed old text from schematic.
    [MoonStalker.sch]
2016-04-24 Added Arduino sketchbook
2016-04-28 Added document which describes Moonstalker-Arduino messages for communication
2016-10-02 Removed ArduinoDebug class
2016-11-20 Added some more PCB stuff.
2016-12-31 Generated netlist and started associating symbols to footprints.
    [MoonStalker.sch]
2016-12-31 Added footprints for Arduino Micro and Pololu DRV8825.
    [MoonStalker.sch]
2017-01-07 Finished schematic, footprints and cvpcb associations. Netlist complete and ready for PCB layout.
    [MoonStalker.sch]
2017-01-08 Started pcb layout. A lot of work already done.
    [MoonStalker.kicad_pcb]
2017-01-08 Finished all connections in the pcb layout. Still have to check all DRC rules, add OSHPark limits, make some tracks thicker.
    [MoonStalker.kicad_pcb]
2017-01-13 Adjusted all track widths and design rules for Osh Park. Mounting holes still missing.
    [MoonStalker.kicad_pcb]
2017-03-11 Added mounting holes and silkscreen logo to the PCB.
    [MoonStalker.kicad_pcb]
2017-03-12 Made the RefDes for mounting holes invisible.
    [MoonStalker.kicad_pcb]
2017-03-12 Moved some RefDes around, they were wrongly positioned. Generated files for manufacturing in gerbers directory.
    [MoonStalker.kicad_pcb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]
2017-03-12 Added BOM.
2017-03-28 Started working on Arduino code.
2017-03-29 Updated R1 and R2 resistor values to real measured values.
    [MoonStalker.sch]
2018-07-31 Framework change in AsyncTasks.
2019-02-27 Started Arduino SW implementation.
2019-03-02 Arduino SW implemented further.
2019-03-03 Added pin initialization.
2019-03-06 Now using two timers.
2019-03-06 moonstalker v 2.0
    [app_bar_main.xml]
2019-03-07 Fixed a bug where the current step was not initialized to zero for horizontal and vertical. Added printout for the initial ocrxa values.
2019-03-10 Fixed battery voltage calculation.
2019-03-12 Implementation of move fragment.
    [app_bar_main.xml]
2019-03-24 Stepper data saved into documuntation.
2019-04-04 APKs for MoonStalker and Arduino Emulator
2019-04-06 Nekaj sprememb v GUI
    [app_bar_main.xml]
2019-04-06 Removed mv text from battery voltage report.
2019-04-07 Integracija s: HW. messages...
    [app_bar_main.xml]
2019-04-29 GUI predelan
    [app_bar_main.xml]
2019-05-06 Fix in arduino emulator for voltage.
2019-05-06 Arduino emulator build.gradle.
2019-05-06 encodings for arduino emulator
2019-05-06 project changes for arduino emulator
2019-05-06 Upgreaded framework.
    [app_bar_main.xml]
2019-07-21 Modifying Drive SW. Adding class StepperController.
2019-07-23 Fixed the register value calculation.
    [StepperController.cpp]
2019-09-23 Verzija 3.0
    [app_bar_main.xml]
2019-09-24 Version 3.0
    [app_bar_main.xml]
2020-02-02 Updated UI.
    [app_bar_main.xml]
2020-04-28 Added test sketch for stepper motors.
2020-05-09 Dodana knjiznica za vektorsko grafiko SVG. SVGResources fix.
    [app_bar_main.xml]
2020-08-28 Upgraded to higher version of Android studio
    [app_bar_main.xml]
2026-06-05 Added limit switch support
2026-06-15 UI-UX refactorisation.
    [app_bar_main.xml]
2026-06-25 Adding testing gui for sending commands to arduino
